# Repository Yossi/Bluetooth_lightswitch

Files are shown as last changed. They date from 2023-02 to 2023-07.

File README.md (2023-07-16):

# Bluetooth lightswitch
The goal of this project is to create remote control capability for a lightswitch in a room without depending on line-of-sight or the uptime of a LAN. All while maintaining normal functionality of the lightswitch.
Bluetooth is perfect for this.

The project consists of two parts: the actual hardware in the wall, and the somewhat optional custom app to control it with.

This documentation is intended as an overview, not necessarily as a strict roadmap to be followed exactly as I did it.
## Hardware
The hardware consists of a Raspberry PiPico with a bluetooth daughterboard (I used an HC-06) and a relay and a USB power source all embedded inside the electrical box where the switch is. This can get rather tight and in my case I had to replace the existing 1 gang box with a 2 gang box to make things fit. The switch itself had to be replaced with a 3-way switch and the relay (mounted right behind the switch) acts as the other switch in the set. If either is toggled, the lights change state.  
diagram of 3 way switch  
Gif by Cburnett, CC BY-SA 3.0, https://commons.wikimedia.org/w/index.php?curid=2426609

### PiPico
I used an original PiPico (not the W version) because that's all that was out at the time. It's possible the PiPicoW will soon have bluetooth support turned on, need to revisit when that happens.
### Bluetooth board
I used an HC-06 board. To change the device name and pin use the commented out code in the vicinity of line 30 in `main.py`
### Relay
Get a relay board, not just a raw relay. Make sure the relay is rated to handle wall voltage (120VAC) and that the board runs on 5vDC (eg. not 12v) since that's available on the PiPico directly from USB power.
Relay boards come in various configurations. Some want a constant signal to hold the relay closed, and release it when the signal goes low. Others toggle on or off when a pulse comes along the signal wire. On with an off pulse, or off with an on pulse. Some even have a jumper to change how they behave. What pin you connect the signal line to depends on how your board works. (blue wire in the diagram). See `main.py` (line 13-ish) for what's what.

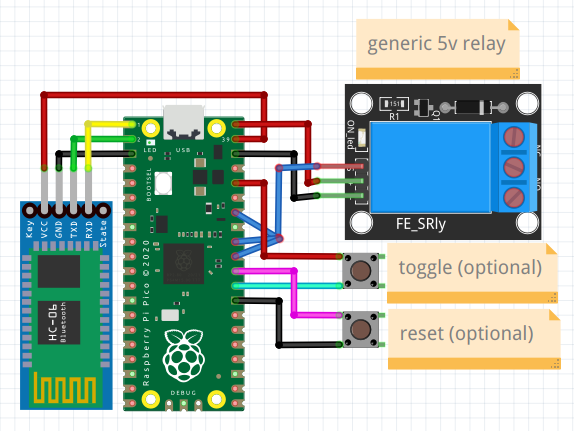
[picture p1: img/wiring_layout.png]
wiring diagram

### USB Power
I tried to find/build various ways to turn 120vAC into 5vDC but the safest, easiest way is to get the smallest USB wall brick you can find (like what apple makes) and the smallest 2 prong socket (like something cut off the end of a string of holiday lights) and wire up a plug inside the gang box. Some setups are harder/impossible to get 120v power from witout making the lights be always on. Hope you don't have one of those setups.
### 2 Gang Box
My 1 gang box didnt have enough room to cram all this inside so I had to replace it with a 2 gang box [like this](https://www.youtube.com/watch?v=1bre8JtsUXI). Other styles of old work box exist, you can find videos on how to install them if needed.
#### Faceplate
I got a 2 switch plate and a filler for the unused one because those are easier to find than a switch and blank. Plus "switch and blank" plates have screw placement that is unpleasing.
### 3 Way Switch
Try to get one that has minimal volume in back to leave room for the relay.
### Wires and connectors
For wires, I happened to find a couple feet of scrap Romex on the side of the road so I used some of the 14 gauge from that to wire the relay to my 3 way switch.  
For connectors, do yourself a favor and get Wago lever nuts. Twist nuts and other garbage can work too.
## App
To remotely toggle the relay you need an app that sends the character '1' over bluetooth.  
[Serial Bluetooth Terminal](https://play.google.com/store/apps/details?id=de.kai_morich.serial_bluetooth_terminal&hl=en_US&gl=US) is good enough to get started. You can set one of the buttons at the bottom to read [Toggle] and make it send a '1'.  
Or you can use the app I slapped together in [AppInventor](http://ai2.appinventor.mit.edu). The .aia file is in the AndroidApp folder.

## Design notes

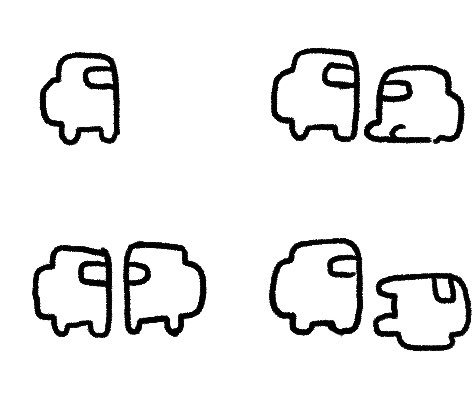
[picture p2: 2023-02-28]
AndroidApp/assets/d6e.jpg

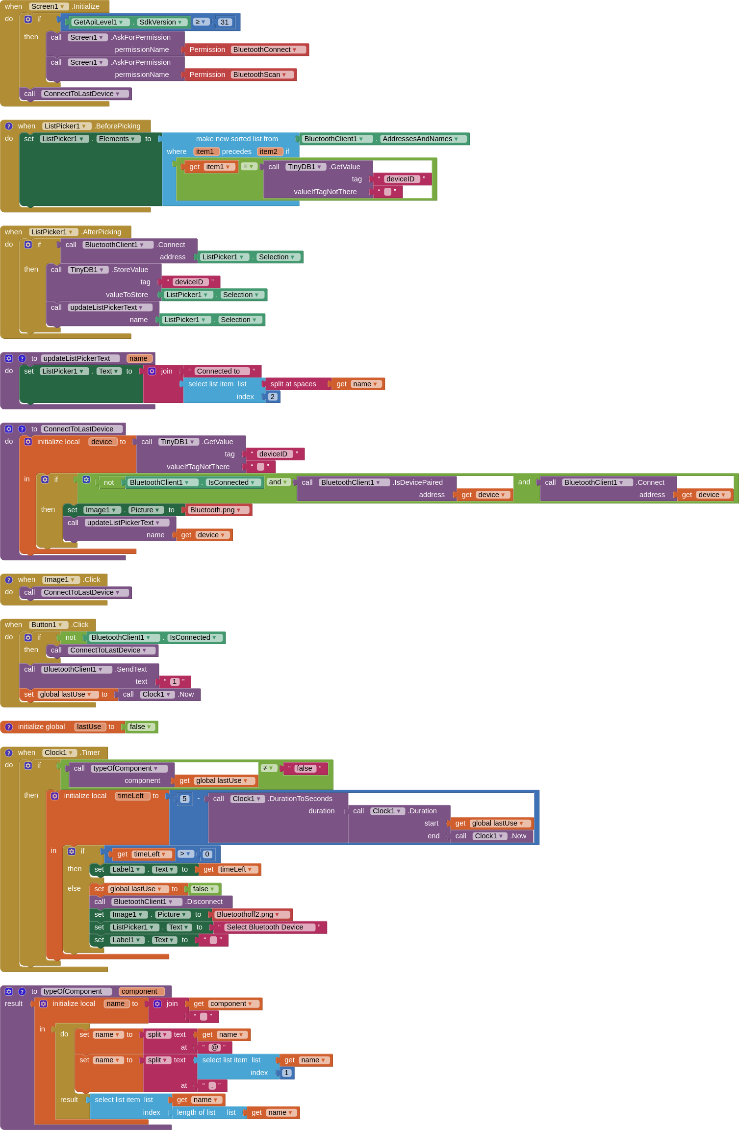
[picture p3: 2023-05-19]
AndroidApp/blocks.png

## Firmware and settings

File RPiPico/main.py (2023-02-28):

from machine import UART, Pin
import time

def pulse(pin):
    pin.toggle()
    time.sleep(0.1)
    pin.toggle()

# if your relay board needs a constant signal to remain switched, connect it to pin 28
relay1 = Pin(28, Pin.OUT)
relay1.off()
# if your relay board needs a pulse to toggle
# connect it to pin 27 for always low or 26 for always high
relay2 = Pin(27, Pin.OUT)
relay2.off()
relay3 = Pin(26, Pin.OUT)
relay3.on()

# optional manual toggle button. button momentarily connects pin 22 to V+
button = Pin(22, Pin.IN, Pin.PULL_DOWN)
# you can also optionally put a button between RUN and GND to reset the pico and usually reset the relay too.

uart = UART(0, baudrate=9600, tx=Pin(0), rx=Pin(1))

''' # this gets flashed to the HC-06 so only needs to happen once
# HC-06 is receptive to AT commands so long as nothing is connected to it over Bluetooth

name = b'lights'
pin = b'1111'

uart.read(uart.write(b'AT+NAME%s\r\n' % name))
uart.read(uart.write(b'AT+PIN%s\r\n' % pin))
'''

uart.write("Starting Application\r\n")

while True:
    if button.value():
        relay1.toggle()
        pulse(relay2)
        pulse(relay3)
        time.sleep(0.5)
        print("Button toggle")

    if uart.any() > 0:
        rxData = uart.read(1);
        if "1" in rxData:
            uart.write("Toggling\r\n")
            relay1.toggle()
            pulse(relay2)
            pulse(relay3)
            print("Bluetooth Toggle")

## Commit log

2023-02-28 Add another relay type and rearrange some pins
2023-03-04 Add timer countdown display
    Also reduce countdown to 5 seconds
2023-05-19 Add fzz file used to create image in readme
    [wiring layout.fzz]
2023-05-19 Auto reconnect when button pushed
    Also grey out bluetooth icon when disconnected.
